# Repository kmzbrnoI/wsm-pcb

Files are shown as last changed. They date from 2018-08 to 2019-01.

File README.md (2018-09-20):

# WSM-PCB: A Wireless SpeedoMeter PCB

WSM is a model railroad car which measures speed of a train and transmits it via
Bluetooth. This repository contains schematics & PCBs layout for all the PCBs
used in the car.

The whole car is designed to be supplied by any 3.7V LiPo battery. PCB design
allows you to charge the battery via USB, so no disconnecting of the battery
nor external changer is required. The measurement is based on an opto-sensor
capturing a perforated wheel connected to an axis of a wheel of the car. The
speed-data are transmitted via HC-05 bluetooth module to any device supporting
SPP bluetooth profile.

This solution consists of a main board (`main-board.{brd,sch}`) and board
for connecting the optosensor (`opto-con.{brd,sch}`). Main board contains all
the logic, optosensor connector board contains no logic, it serves only for
mechanical purposes. Optosensor connector board is not required.

## Features

 * Speed-measuring based on opto-sensor.
 * Size 50×18 mm.
 * Transmits data via bluetooth.
 * No external power supply is required (no current from tracks).
 * Runs on battery, can measure up to 8 hours based on chosen battery.
 * Integrated charging circuit.
 * Charging from micro-USB connector.
 * ON/OFF switch.
 * Measuring of a battery level & undervoltage protection.

## Resources

 * [Firmware to the main CPU](https://github.com/kmzbrnoI/wsm-fw).
 * [Software to PC](https://github.com/kmzbrnoI/wsm-speed-reader).

## Toolkit

This PCB was designed in Eagle 9.

## Sensor

This boards was tested with
[GP1S23 opto sensor](http://static6.arrow.com/aropdfconversion/33ee6367e3f24c1538ff4b63e7c9272b758d9d51/tec_datasheet_gp1s23.pdf).
This sensor in commonly available at KY-010 Arduino module.

## Mechanics

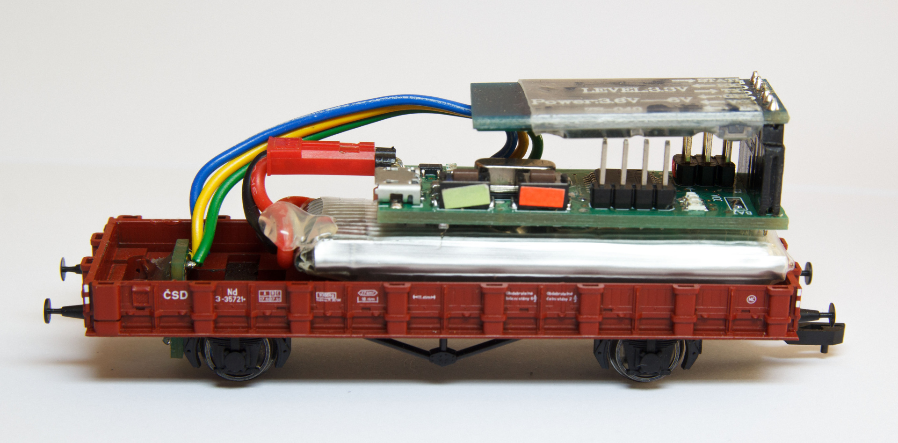
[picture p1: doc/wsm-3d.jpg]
A WSM prototype 3D

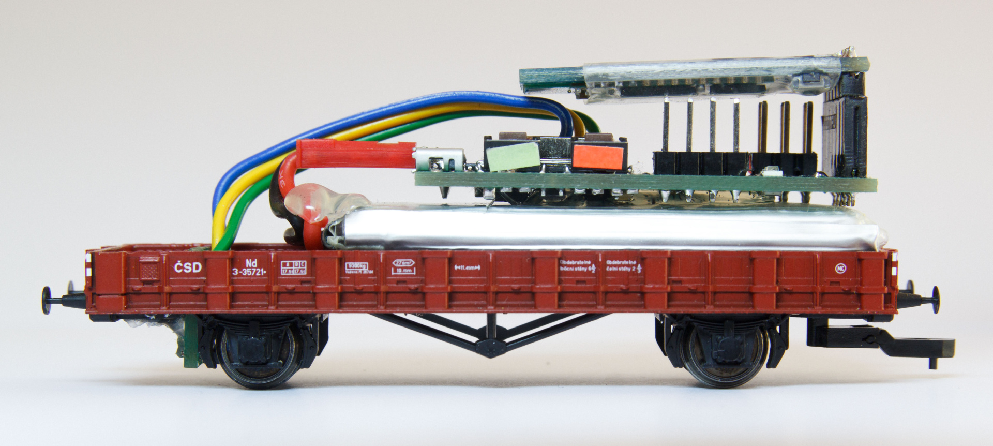
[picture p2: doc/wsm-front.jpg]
A WSM prototype front

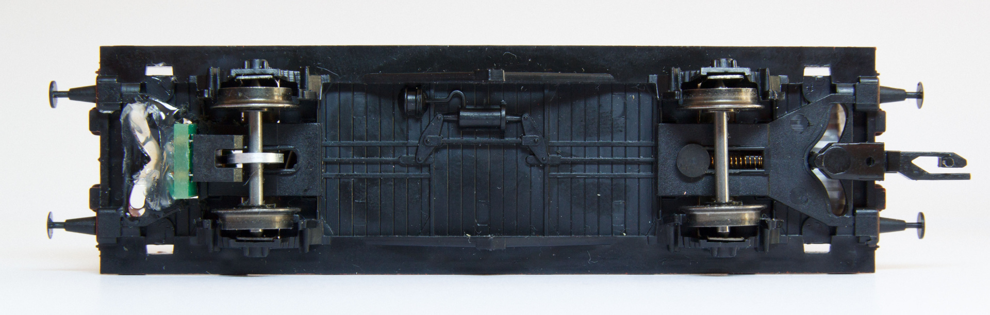
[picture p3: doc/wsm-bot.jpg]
A WSM prototype bottom


## `place.tex`

This TeX file allows you to merge top and bottom place layouts into a single
document.

## Authors

 * Jan Horacek ([jan.horacek@kmz-brno.cz](mailto:jan.horacek@kmz-brno.cz))

## Credits

 * This project is inspired by the measure car designed by *Petr Travnik*.
 * The ON-OFF switch part is inspired by the RB3201 project of *[RoboticsBrno
   ](https://github.com/RoboticsBrno)*.
 * Many thanks to *Michal Petrilak* for help with development of this project.

## License



This project is released under the [Creative Commons Attribution-ShareAlike 4.0
](https://creativecommons.org/licenses/by-sa/4.0) license.

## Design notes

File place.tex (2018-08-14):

\documentclass[a4paper]{article}
\usepackage[czech]{babel}
\usepackage[utf8]{inputenc}
\usepackage{graphicx}
\setlength{\textheight}{29cm}
\setlength{\textwidth}{13cm}
\pagestyle{empty}
\setlength{\unitlength}{1mm}

\begin{document}
\noindent
\begin{center}

\huge WSM-PCB place \\
\large v1.2 \\
\normalsize JH 2018
\end{center}

\begin{picture}(200,250)(23,5)
\put(-25, -30){}
\put(-25,-100){}
\end{picture}

\end{document}

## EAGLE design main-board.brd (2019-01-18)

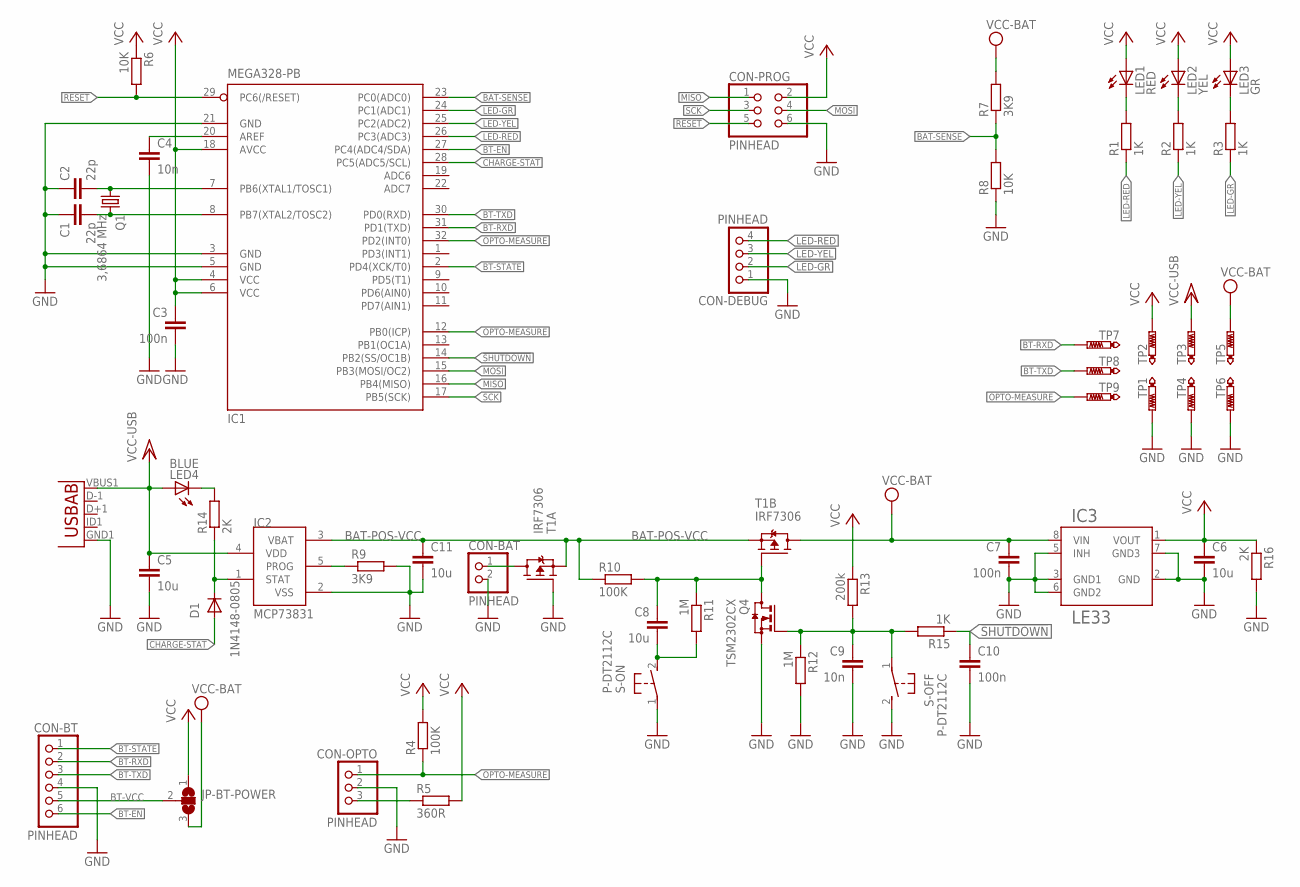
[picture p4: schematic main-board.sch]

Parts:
C1, C2: 22p; C0805
C3, C7, C10: 100n; C0805
C4, C9: 10n; C0805
C5, C6, C8, C11: 10u; C0805
CON-BAT: PINHEAD; 1X02
CON-BT: PINHEAD; 1X06
CON-DEBUG: PINHEAD; 1X04
CON-OPTO: PINHEAD; 1X03
CON-PROG: PINHEAD; 2X03
D1: 1N4148-0805; R0805
IC1: MEGA328-PB; TQFP32-08
IC2: MCP73831; SOT23-5L
IC3: LE33; SO08
JP-BT-POWER: SJ2W; SJ_2
LED1: RED; CHIP-LED0805
LED2: YEL; CHIP-LED0805
LED3: GR; CHIP-LED0805
LED4: BLUE; CHIP-LED0805
Q1: 3,6864 MHz; HC49UP
Q4: TSM2302CX; SOT23
R1, R2, R3, R15: 1K; R0805
R4, R10: 100K; R0805
R5: 360R; R0805
R6, R8: 10K; R0805
R7, R9: 3K9; R0805
R11, R12: 1M; R0805
R13: 200k; R0805
R14, R16: 2K; R0805
S-OFF: P-DT2112C; DTSM-3
S-ON: P-DT2112C; DTSM-3
T1: IRF7306; SO08-IRF
TP1, TP2, TP3, TP4, TP5, TP6, TP7, TP8, TP9: PTR1B1,27; B1,27
U1: USB""; USB-MICRO-SMD

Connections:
!RESET: CON-PROG.5, IC1.29 (PC6(/RESET)), R6.2
!SHUTDOWN: C10.1, IC1.14 (PB2(SS/OC1B)), R15.1
!SHUTDOWN_INT: C9.1, Q4.1 (G), R12.1, R13.2, R15.2, S-OFF.1
BAT-POS-VCC: C11.1, IC2.3 (VBAT), R10.1, T1.1 (S), T1.3 (S)
BAT-RAW-VCC: CON-BAT.1, T1.7 (D), T1.8 (D)
BAT-SENSE: IC1.23 (PC0(ADC0)), R7.1, R8.2
BT-EN: CON-BT.6, IC1.27 (PC4(ADC4/SDA))
BT-RXD: CON-BT.2, IC1.31 (PD1(TXD)), TP7.PP
BT-STATE: CON-BT.1, IC1.2 (PD4(XCK/T0))
BT-TXD: CON-BT.3, IC1.30 (PD0(RXD)), TP8.PP
BT-VCC: CON-BT.5, JP-BT-POWER.2
CHARGE-PROG: IC2.5 (PROG), R9.1
CHARGE-STAT: D1.A, IC1.28 (PC5(ADC5/SCL))
CHARGE-STAT-INT: D1.K (C), IC2.1 (STAT), R14.1
CHARGE-STAT-LED: LED4.C, R14.2
CPU-REF: C4.1, IC1.20 (AREF)
CR1: C1.2, IC1.8 (PB7(XTAL2/TOSC2)), Q1.2
CR2: C2.2, IC1.7 (PB6(XTAL1/TOSC1)), Q1.1
GND: C1.1, C2.1, C3.2, C4.2, C5.2, C6.2, C7.2, C9.2, C10.2, C11.2, CON-BAT.2, CON-BT.4, CON-DEBUG.1, CON-OPTO.2, CON-PROG.6, IC1.3 (GND), IC1.5 (GND), IC1.21 (GND), IC2.2 (VSS), IC3.2 (GND), IC3.3 (GND1), IC3.5 (INH), IC3.6 (GND2), IC3.7 (GND3), Q4.2 (S), R8.1, R9.2, R12.2, R16.2, S-OFF.2, S-ON.1, T1.2 (G), TP1.PP, TP4.PP, TP6.PP, U1.GND1 (GND)
LED-GR: CON-DEBUG.2, IC1.24 (PC1(ADC1)), R3.1
LED-GR-R: LED3.C, R3.2
LED-RED: CON-DEBUG.4, IC1.26 (PC3(ADC3)), R1.1
LED-RED-R: LED1.C, R1.2
LED-YEL: CON-DEBUG.3, IC1.25 (PC2(ADC2)), R2.1
LED-YEL-R: LED2.C, R2.2
MISO: CON-PROG.1, IC1.16 (PB4(MISO))
MOSI: CON-PROG.4, IC1.15 (PB3(MOSI/OC2))
OPTO-MEASURE: CON-OPTO.1, IC1.12 (PB0(ICP)), IC1.32 (PD2(INT0)), R4.1, TP9.PP
OPTO-VCC: CON-OPTO.3, R5.1
SCK: CON-PROG.3, IC1.17 (PB5(SCK))
START_BUTTON: C8.2, R11.2, S-ON.2
START_GATE: C8.1, Q4.3 (D), R10.2, R11.1, T1.4 (G)
VCC: C3.1, C6.1, CON-PROG.2, IC1.4 (VCC), IC1.6 (VCC), IC1.18 (AVCC), IC3.1 (VOUT), JP-BT-POWER.1, LED1.A, LED2.A, LED3.A, R4.2, R5.2, R6.1, R13.1, R16.1, TP2.PP
VCC-BAT: C7.1, IC3.8 (VIN), JP-BT-POWER.3, R7.2, T1.5 (D), T1.6 (D), TP5.PP
VCC-USB: C5.1, IC2.4 (VDD), LED4.A, TP3.PP, U1.VBUS1 (VBUS)

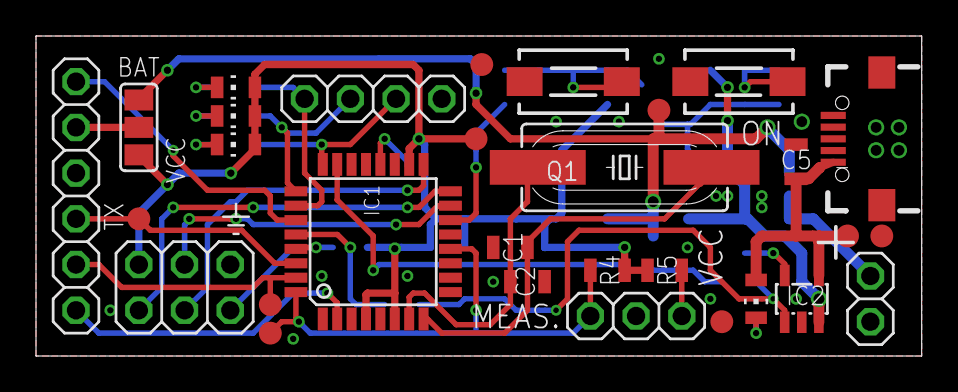
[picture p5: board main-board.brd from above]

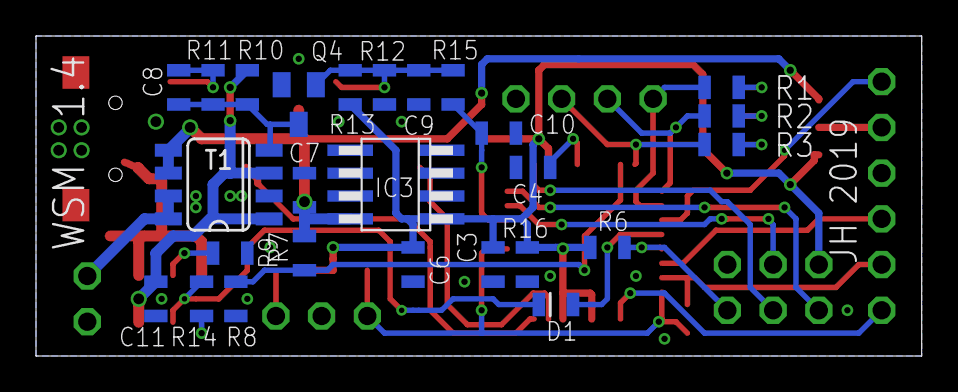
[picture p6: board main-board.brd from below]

Board: 2 copper layers, 49.2 x 17.8 mm, 56 parts (26 on the bottom side), 35 nets.

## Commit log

2018-07-11 Initial commit.
    [merici-vuz.sch]
2018-07-11 Add first parts of schematics.
    [merici-vuz.sch]
2018-07-11 Another improvements.
    [merici-vuz.sch]
2018-07-12 Add LE33 LDO.
    [merici-vuz.sch]
2018-07-12 Add power control of peripherals.
    [merici-vuz.sch]
2018-07-12 Add power jumper.
    [merici-vuz.sch]
2018-07-12 Add LED to charging circuit.
    [merici-vuz.sch]
2018-07-13 Eagle 9.0 & on & off buttons.
    [merici-vuz.sch]
2018-07-13 Reset -> !reset.
    [merici-vuz.sch]
2018-07-13 Fix unconnected LEDS.
    [merici-vuz.sch]
2018-07-13 Add connector for debug measuring.
    [merici-vuz.sch]
2018-07-13 Decrease current to !SHUTDOWN to 10 mA.
    [merici-vuz.sch]
2018-07-13 Add polarity protection.
    [merici-vuz.sch]
2018-07-13 Add missing wires & edit debug connector.
    [merici-vuz.sch]
2018-07-13 Add names to signals.
    [merici-vuz.sch]
2018-07-13 Unify names of resistors & capacitors.
    [merici-vuz.sch]
2018-07-14 Faster on & off switches.
    [merici-vuz.sch]
2018-07-14 Add net classes.
    [merici-vuz.sch]
2018-07-14 Remove unwanted VCC/2.
    [merici-vuz.sch]
2018-07-14 Board: initial commit.
    [merici-vuz.brd]
2018-07-14 First prototype of PCB.
    [merici-vuz.brd, merici-vuz.sch]
2018-07-14 Board: pads, minor improvements.
    [merici-vuz.brd]
2018-07-14 Board: center pinheaders.
    [merici-vuz.brd]
2018-07-14 Board: add texts for silkscreen.
    [merici-vuz.brd]
2018-07-14 Version 1.1.
    [merici-vuz.brd, merici-vuz.sch]
2018-07-14 Add optoconnector PCB.
    [opto-con.brd, opto-con.sch]
2018-07-15 Move some wires to make schematics more clear.
    [merici-vuz.sch]
2018-07-15 BT takes power from VCC-BAT, not BAT-POS-VCC.
    [merici-vuz.brd, merici-vuz.sch]
2018-07-15 Add min. drill size to net classes.
    [merici-vuz.brd, merici-vuz.sch]
2018-07-15 Change shape of pins on pinheaders.
    [merici-vuz.brd, merici-vuz.sch]
2018-07-15 Rename main board.
    [main-board.brd, main-board.sch]
2018-07-16 Optimize for BOM.
    [main-board.brd, main-board.sch]
2018-07-19 Con-bt-power -> jumper BT power.
    [main-board.brd, main-board.sch]
2018-07-19 Connect OPTO-MEASURE to ICP (PB0).
    [main-board.brd, main-board.sch]
2018-07-19 Move CHARGE-STAT to digital pin.
    [main-board.brd, main-board.sch]
2018-07-19 Schematics: move power parts together.
    [main-board.sch]
2018-07-19 Fix polarity-protection MOSFET.
    [main-board.brd, main-board.sch]
2018-07-20 Add diode to CHARGE-STAT pin.
    [main-board.brd, main-board.sch]
2018-07-21 Change value of C9.
    [main-board.brd, main-board.sch]
2018-07-22 Use SJ2W for BT power switching.
    [main-board.brd, main-board.sch]
2018-07-22 Add 'basic' & 'debug' assembly variants.
    [main-board.brd, main-board.sch]
2018-07-30 Update drill in micro-USB connector.
    [main-board.brd, main-board.sch]
2018-07-30 Edit names for silkscreen.
    [main-board.brd, main-board.sch]
2018-07-30 Update active layers to default.
    [main-board.brd]
2018-08-14 Create nice place views.
    [main-board.brd, main-board.sch]
2018-08-18 Fix shutdown circuit.
    Shutting down from CPU should work now.
    [main-board.brd, main-board.sch]
2018-08-18 Change voltage divisor (use LDO as reference).
    [main-board.brd, main-board.sch]
2018-08-28 4K -> 3K9.
    [main-board.brd, main-board.sch]
2018-08-29 Add silkscreen for PCB manufacturing.
    [main-board.brd]
2018-08-29 Update values of resistors.
    [main-board.brd, main-board.sch]
2018-08-29 Fix placing.
    [main-board.brd]
2018-08-29 Show default layers.
    [main-board.brd]
2018-09-20 Write meaning of measure signals to silkscreen.
    [main-board.brd, opto-con.brd]
2018-12-30 Set R4 to 100k.
    The construction of second protoype showed that the value of the pull-up
    is critical for proper device function.
    [main-board.brd, main-board.sch]
2019-01-18 Protect charging circuit against polarity change too.
    [main-board.brd, main-board.sch]
2019-01-18 Decrease mdCopperDimension to 10 mil.
    [main-board.brd]
2019-01-18 Remove wire stubs, make LED's pads smaller.
    [main-board.brd, main-board.sch]
2019-01-18 Adjuct place a little.
    [main-board.brd]
